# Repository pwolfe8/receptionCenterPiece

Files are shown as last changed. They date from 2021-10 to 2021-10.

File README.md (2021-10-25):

# Reception Center Piece
This was the planetary gear center piece that I designed & implemented for my reception. 

This repo is a way to share design files and provide an assembly tutorial for those who want to use this for their own reception, fork off the design, or just print their own copy of this cool decoration piece. 

## Clone this repository
Open a terminal wherever you want to place this folder. Then clone this repository and the webrepl submodule with:
```bash
git clone https://github.com/pwolfe8/receptionCenterPiece
cd receptionCenterPiece
git submodule update --init --recursive
```
___
## Mechanical
I printed this on a Prusa i3 MK3S. The trays and all the settings are in the `print_trays` folder.
I printed with [standard 1.75mm black PETG filament](<https://www.amazon.com/dp/B08XGX23TP?psc=1&ref=ppx_yo2_dt_b_product_details>) on a textured prusa print tray. 

Approximate total print time: ~19 hrs depending on heating/cooling time.

Design files can be found on Onshape: 
- [fullDesignReception](<https://cad.onshape.com/documents/7be5b9b09e066ba446a30efc/w/afbadb4d389ea6207fcba0bc/e/a346c253faa0d5286ebe5b9c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>)
- [AA_3V_Boost5V](<https://cad.onshape.com/documents/a1963687730519ec8fcaa736/w/4932db5a468bc2b8e7c12e8f/e/31f6f86f6f40c3d5acde4a41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>)

screw bolts/nuts used:
- 2x M2x8 screws ([here's](<https://www.amazon.com/gp/product/B07F739QCM/ref=ppx_yo_dt_b_search_asin_title?ie=UTF8&th=1>) the metric screw bolt/washer/nut kit I used. good to have around for various projects)
- 2x M2 nuts from same kit
- the small philips head screw that came with the microservo

## Painting & Decoration
I did not do the painting/decoration my wife and her sister did. My wife also came up with the concept. 

The premise for painting was paint a thin copper layer leaving some black showing underneath to look like worn copper for more of a steampunk feel. 
DO NOT print the smooth interface between the ring gear and the sun/planetary gears as it will add too much friction to move easily. 

Here's a quick DO NOT paint list: 
- bottom of planetary gears
- bottom of sun gear
- part of ring gear touching the bottom of the planetary/sun gears
- the base drive gear & anything used to hold it in place as it's hidden underneath anyways
- the servo horn attachment (it's hidden as well)

Decoration involved several amazon and hobby lobby items and is really up to you. [insert picture here later of ours decorated]

## Electrical

Wanted to try out micropython so I got these [D1 Mini modules](<https://www.amazon.com/dp/B08QZ2887K?psc=1&ref=ppx_yo2_dt_b_product_details>) based on the ESP8266 and flashed them with the latest version. They averaged 3 dollars each at the time I purchased them. 

If you just care about You can use any microcontroller and make your own electronics box for it as long as
- powerable off 5V since that's what the boost converter output is. (and servo needs 5V pwr). though you could power off 3V directly from battery if you modify the circuit
- has a pwm pin to drive servo

Anyways here's the parts list to make a single center piece: 
- 1x [microcontroller](<https://www.amazon.com/dp/B08QZ2887K?psc=1&ref=ppx_yo2_dt_b_product_details>) (D1 mini)
- 1x [micro servo](<https://www.amazon.com/dp/B07L2SF3R4?psc=1&ref=ppx_yo2_dt_b_product_details>) (modified for continuous rotation. you can just buy one that's continuous to make your life easier. only slightly pricier though. In the improved version I will make it based off of a continuous one.)
- 1x [5V 1A boost converter](<https://www.adafruit.com/product/4654>)(adafruit/digikey): This might've been more current than needed, but was better to be safe for a rapid prototype)
- 1x [mechanical switch](<https://www.adafruit.com/product/3221>)(adafruit): just a cool clickly mechanical switch
- 2x [battery contact positive](<https://www.digikey.com/en/products/detail/mpd-memory-protection-devices/SN-T5-2/2439587>)(digikey)
- 2x [battery contact negative](<https://www.digikey.com/en/products/detail/mpd-memory-protection-devices/SN-T5-1/2439583>)(digikey)
- the screw bolts/nuts listed in the mechanical section

and here's the schematic (full fritzing file in the circuit folder): 
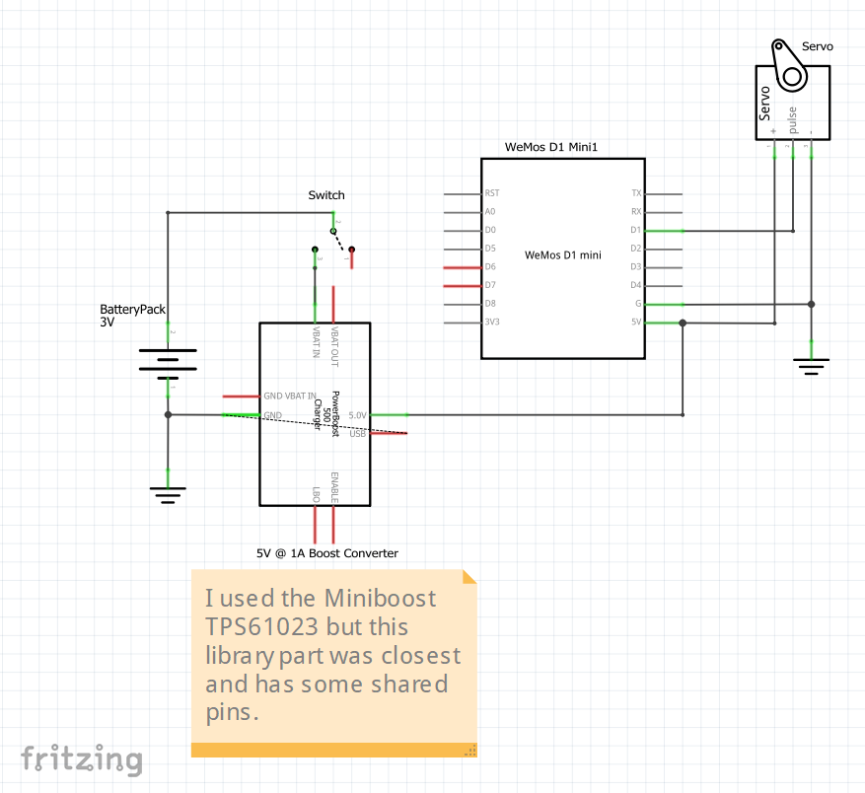
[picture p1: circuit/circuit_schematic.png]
circuit_schematic


### Servo Modification for Continuous Rotation

I was a dumbass and bought normal servos with limited range. For a little more money you can buy continuous servos in the same shape. I will post a link once I try some to make sure they have the same dimensions...

But if you really don't want to wait, here's a guide on what I did to modify the servo and the servo horn:
Maybe wear gloves to avoid silicon grease on you.
- unscrew the 4 screws
- place the gears out in the order you took them off so you don't forget
- remove the metal blocking component off the potentiometer
- replace the gears in order except the last top one
- clip the plastic blocking part off with flush cutters and smooth with exacto knife
- replace top gear and screw back together
- then take the cross shaped servo horn and chip away until you snip off the long sides with flush cutters. then make a smooth curve with flush cutters.
- use the small philips screw to hold the horn in

## Firmware/Software
[This Guide](software/D1_tutorial.md) will show you how to install the tools to flash and setup your D1 Mini for over the air updates.

I also included the version of micropython I used for this board already downloaded in the software folder [here](software/esp8266-20210902-v1.17.bin). Follow the guide to flash it on your board and send over the main.py for this center piece heartbeat pulse code.

___
## Assembly
Once you have all the pieces printed, follow this guide on assembly.
Note: pull up the onshape as a visual reference for the fully assembled piece. feel free to hide/show parts to see internals if it's unclear.

### Mechanical Assembly

Clean up the brims off all the pieces, especially the gears that will be interfacing with other gears. If you experience jamming it's probably because you haven't fully cleaned the brim off every tooth of one of the gears.

First assemble the base & motor box:
- get the base support piece and the motor box and pegs.
- align the motor box appropriately to base following the onshape design.
- now make sure the motor box and base have a shared flat surface on the bottom. feel free to put on a table to see if it's level
- then push/wiggle the pegs into place (friction fit) to hold the motor box to the base. you may have to sand/trim the hole/pegs
- Now attach the servo motor with M2 screws/nuts. I used M2x8 but you can take up to M2x12 as well. screw head coming from underneath motor box and nut on top of motor.  
NOTE: there are 2 orientations, make sure the way you choose gets the servo horn aligned with the center of the box. Not the other way
- now undo the small philips head on the servo, put the gear attachment over the servo horn, and then screw the small philips back in.

Now assemble the drive gear:
- stack the drive gear + ring gear + sun gear as shown in the cad design files.
- put the drive shaft through such that the top circle stopper is stopped against the sun gear.
- put the locking ring and shaft through to make sure it's held in place. 
- pull the ring gear away from the drive gear so they no longer contact other than by the drive shaft (should be ~2mm gap)

Place the drive gear assembly on the base by aligning the 2 small notches on the outside of the ring gear with the base. If it doesn't fit you've put your motor on in the wrong orientation so reverse/repeat steps to flip it.  Congrats! hard part done

Now assemble the platforms/planetry gear pieces.

Let's assemble the first/shortest platform first.
- find the 3 candle holders, first platform, shortest shaft, and 1 planetary gear
- get the shortest candle holder and place it in first then go clockwise like in the onshape and put the next highest, then tallest in. refer to onshape if you get stuck.
- now put the shortest shaft into the bottom shaft hole.
- then place the planetary gear onto the other side of the shaft

Next 2 platforms are straight forward: 
- get 2nd platform (feel free to hot glue some decorations on first, just make sure it's close enough balanced weight-wise for stability)
- get the middle length shaft and a planetary gear
- insert shaft into 2nd platform shaft hole and planetary gear shaft hole
- repeat for 3rd platform

Now final assembly before electrical box:
- place the 1st platform assembly inbetween sun & ring gear
- place the 2nd platform assembly 120 degrees off in the same manner
- place the 3rd platform assembly 120 degrees off in the same manner

Electrical box:
- make sure the orientation matches the onshape 
- place the switch holder into the groove
- place the battery box in the large rectangle with the boost converter facing out

### Electrical Assembly/Wiring Harness
Sadly I didn't have time to make a pcb with nice connectors and all, so I twisted together some wires and hand soldered the wiring harness.  In the future I'll release a pcb design but for now here's what I did:

tools:
- some 22 gauge solid core wire
- strippers/wire cutters
- soldering iron
- heatshrink/heat gun or lighter 

I got a 22 gauge solid core wire pack with different colors off amazon

Cut the following lengths per color and strip each side:
- white: 4, 6 cm
- red: 4, 4, 6 cm  (strip one side more for twist)
- black: 5, 5, 6, 7 cm (strip one side more for twist)
- blue: 2 cm (strip to 1.5 cm insulation)
- yellow: 4 cm 

now assemble: 
- twist the longer red exposed ends together and solder
- repeat for black
- solder blue wire as battery pack series connection
- solder white wire from pack to switch using 6 cm
- solder black long wire to pack ground
- complete rest of soldering according to the circuit schematic above

afterwards you can use a label maker to label on/off depending on how you wired it to the switch

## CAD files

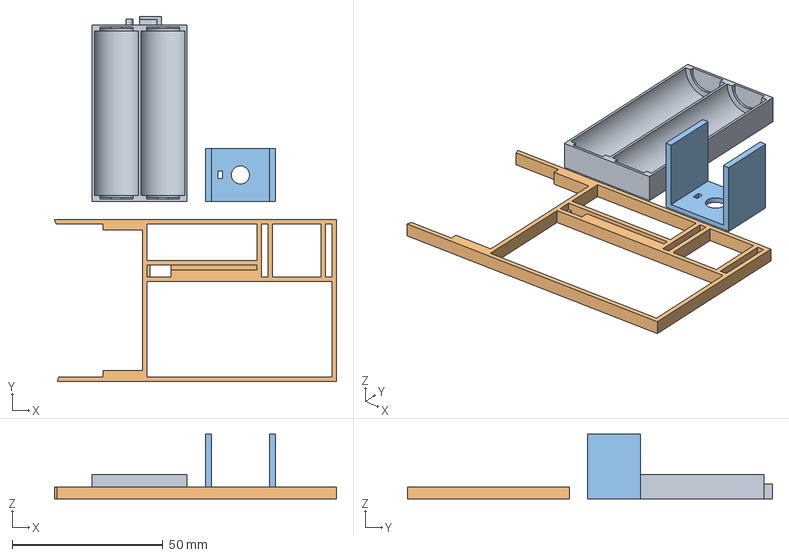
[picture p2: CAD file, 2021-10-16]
print_trays/electrical_1.2hrs_14g.3mf
93.7 x 121.1 x 21.5 mm
AA_3V (2).stl
electrical_box.stl_1
electrical_box.stl_2

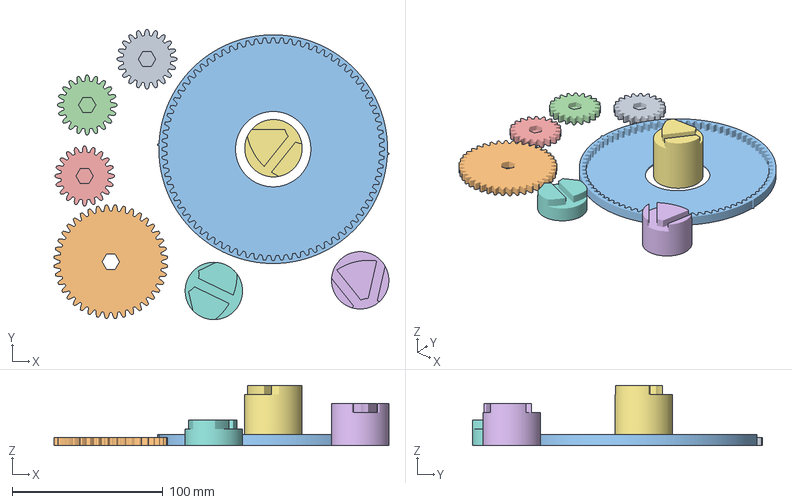
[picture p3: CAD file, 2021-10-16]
print_trays/tray2_6hrs_97g.3mf
222.4 x 192.7 x 40.0 mm
fullDesign (4).stl_10
fullDesign (4).stl_11
fullDesign (4).stl_13
fullDesign (4).stl_17
fullDesign (4).stl_23
candleHolders.stl_1
candleHolders.stl_2
candleHolders.stl_3

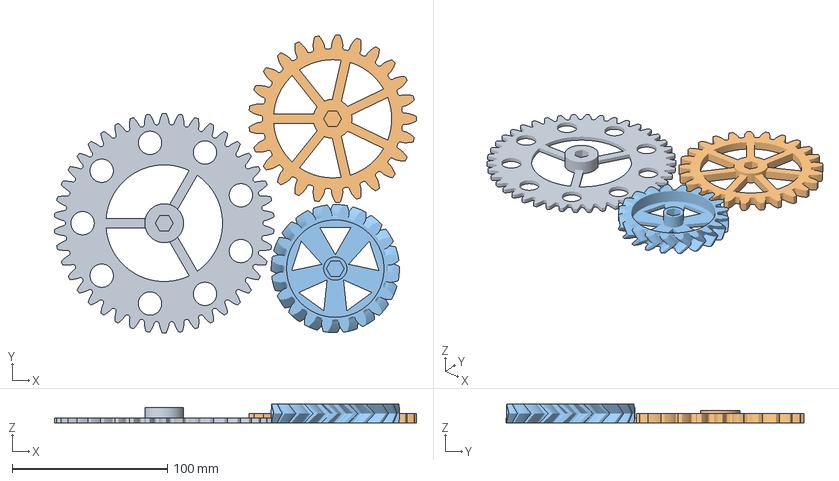
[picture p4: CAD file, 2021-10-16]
print_trays/tray3_5.5hrs_83g.3mf
232.9 x 191.9 x 12.0 mm
fullDesign (4).stl_5
fullDesign (4).stl_6
fullDesign (4).stl_8

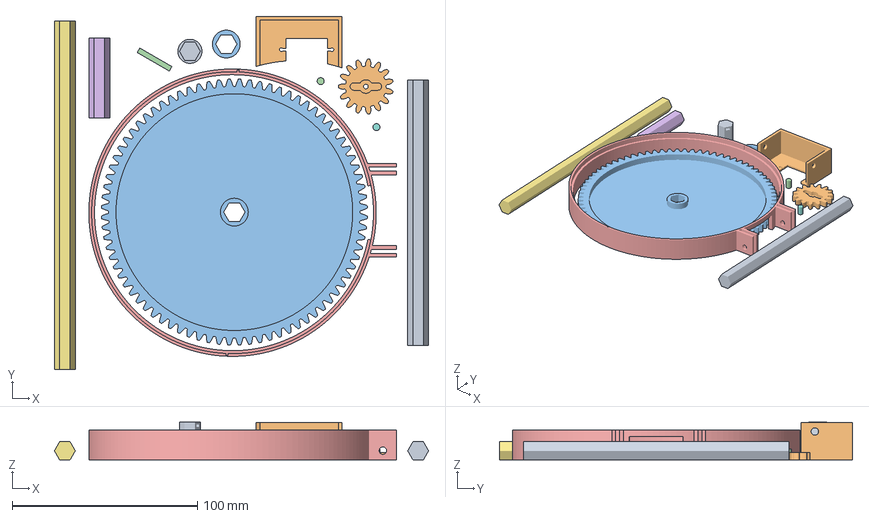
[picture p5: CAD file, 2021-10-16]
print_trays/tray1_6.5hrs_95g.3mf
201.8 x 190.4 x 20.4 mm
fullDesign (4).stl_2
fullDesign (4).stl_3
fullDesign (4).stl_4
fullDesign (4).stl_7
fullDesign (4).stl_12
fullDesign (4).stl_14
fullDesign (4).stl_16
fullDesign (4).stl_18
fullDesign (4).stl_19
fullDesign (4).stl_20
fullDesign (4).stl_21
fullDesign (4).stl_22

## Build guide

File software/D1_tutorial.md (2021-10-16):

# A Quick D1 Mini Micropython Setup/Tutorial

Just my quick reference/cheat sheet for D1 Mini board resources and setting up micropython for updating main.py remotely

## Purchase Source
bought 10 off amazon at ~3 dollars a piece [here](<https://www.amazon.com/dp/B08QZ2887K?psc=1&ref=ppx_yo2_dt_b_product_details>)

## supposed schematic and potential pinout
- https://www.wemos.cc/en/latest/_static/files/sch_d1_mini_v3.0.0.pdf
- https://www.wemos.cc/en/latest/d1/d1_mini.html
- https://escapequotes.net/esp8266-wemos-d1-mini-pins-and-diagram/

## Flashing ESP8266 with Latest Micropython
[tutorial source](<https://www.wemos.cc/en/latest/tutorials/d1/get_started_with_micropython_d1.html>)

Find the latest micropython .bin file in the >4MB flash section and download it [here](<https://micropython.org/download/esp8266/>)
install esptool on your python with `pip install esptool` (github [here](<https://github.com/espressif/esptool>) if you want)

Plug in device via USB and check the port name in device manager (example: COM6)
Now swap PORT_NAME with your port and FIRMWARE.bin with the .bin file you just downloaded in the following commands:
```bash
# first erase flash
esptool.py --port PORT_NAME erase_flash

# then write flash with your preferred firmware .bin file 
esptool.py --port PORT_NAME --baud 115200 write_flash --flash_size=4MB -fm dio 0 FIRMWARE.bin

# here's the example command I used in powershell for the version in this repo. it assumes you're already in the software folder and COM6 is your device serial port
esptool.py --port COM6 --baud 115200 write_flash --flash_size=4MB -fm dio 0 .\esp8266-20210902-v1.17.bin
```

Open [realterm](https://sourceforge.net/projects/realterm/) and set baud to 115200 and open your port. you should be able to type help() and follow the first steps now

## First Steps
```python
# this is how to get help
help()

# this sets up a remote accessible micropython shell
# follow prompts after import to enable webrepl on boot (feel free to reboot)
import webrepl_setup

# this is how to check what files exist on the board
import os
os.listdir()
```

## Network Config
[tutorial source](<https://docs.micropython.org/en/latest/esp8266/tutorial/network_basics.html>)
```python
# turn on client connection and turn off access point
import network
sta_if = network.WLAN(network.STA_IF)
ap_if = network.WLAN(network.AP_IF)
sta_if.active(True)
ap_if.active(False)

# check to be sure they're on/off
sta_if.active()
ap_if.active()

# get mac address
import ubinascii
ubinascii.hexlify(sta_if.config('mac'),':').decode()

# connect to your router's SSID with password now 
sta_if.connect('ssidgoeshere','passwordgoeshere')
# keep checking for a minute until connected
sta_if.isconnected()
# see ip address & network info
sta_if.ifconfig()
```

## webrepl push/pull
navigate your terminal into the webrepl submodule folder first
```bash
# example pull (just pulls the boot.py from remote and saves to local file named "local_boot.py")
python .\webrepl_cli.py -p YOURPASSWORDHERE REMOTEIPHERE:boot.py local_boot.py

# example push (just pushes your local file main.py file located one directory above the cloned webrepl folder to your board and names it main.py)
python .\webrepl_cli.py -p YOURPASSWORDHERE ../software/main.py REMOTEIPHERE:main.py

# feel free to setup batch/bash scripts for your common operations
```

## `main.py` 
micropython executes main.py (if it exists) after boot.py so I generally put my code updates here.
Let's setup an example main.py to turn on the onboard LED. It's connected to GPIO2 according to the D1 Mini Schematic in an active pull down configuration.

Here's an example main.py to turn the LED on on boot

```python
import machine
pin = machine.Pin(2, machine.Pin.OUT)
pin.off()
```

If you want to change the syntax so "on" turns led on use [this documentation](<https://docs.micropython.org/en/latest/library/machine.Signal.html>)

Now use the example push as reference to push this `main.py` file to your board:
```bash
python .\webrepl_cli.py -p YOURPASSWORDHERE ../software/main.py REMOTEIPHERE:main.py
```

To reset your board to let the main.py changes take effect:
- open the webrepl/webrepl.html file in your browser, connect to your W1 Mini's ip address
- type
    ```python
    import machine
    machine.reset()
    ```

Feel free to modify this main.py to your heart's content and push updates/pull current files.
Happy Hacking

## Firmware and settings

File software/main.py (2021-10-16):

# main.py
import machine
import time
import math

servoState = False
servoPulseIdx = 0
threeCountWait = 0

def pulse(l, t):
    for i in range(20):
        l.duty(int(math.sin(i / 10 * math.pi) * 500 + 500))
        time.sleep_ms(t)

def heartbeat(pinpwm, pulseCount):
    heartbeat_delay_ms = 250
    for c in range(pulseCount):
        pulse(pinpwm, 80)
        time.sleep_ms(heartbeat_delay_ms)

def togglepin(p):
    if p.value() == 0:
        p.on()
    elif p.value() == 1:
        p.off()

def debounce(p):
    '''debounce a button pin'''
    window_length_ms = 100
    s = 0
    for i in range(window_length_ms):
        s += p.value()
        time.sleep_ms(1)
    return round(s/window_length_ms)

# def toggleServo():
#     global servoState
#     servoState = not servoState
#     if servoState:
#         servoLEDpin.on()
#     else:
#         servoLEDpin.off()

# def servoButtonCallback(p):
#     val = debounce(p)
#     if val == 0:
#         toggleServo()

def runServoHeartbeat():
    global servoPulseIdx
    global threeCountWait
    if servoPulseIdx >= 20:
        threeCountWait += 1
        # servopwm.duty(0)
        if threeCountWait >= 3:
            threeCountWait = 0
            servoPulseIdx = 0
    else:
        servopwm.duty(int(math.sin(servoPulseIdx / 10 * math.pi) * 500 + 500))
        servoPulseIdx += 1

def blockingHeartbeat():
    pulse(servopwm, 80)

def timerCallback(t):
    blockingHeartbeat()

# onboard LED setup
boardLEDpin = machine.Pin(2, machine.Pin.OUT)
boardLEDpin.off() # this turns on board LED since active low

# servo button, led, and pwm setup
# servobutton = machine.Pin(12, machine.Pin.IN, machine.Pin.PULL_UP)
# servobutton.irq(trigger=machine.Pin.IRQ_FALLING, handler=servoButtonCallback)
# servoLEDpin = machine.Pin(13, machine.Pin.OUT)
# servoLEDpin.off() # active high. start off though.
servopwm = machine.PWM(machine.Pin(5), freq=50) # GPIO5 is D1 on the mini

# servo timer loop setup
servoLoopPeriod_ms = 1850
servoTimer = machine.Timer(-1)
servoTimer.init(period=servoLoopPeriod_ms, mode=machine.Timer.PERIODIC, callback=timerCallback)

### heartbeat tests ###
# pulseCount = 25
## led heartbeat test
# ledpwm = machine.PWM(ledpin, freq=50)
# heartbeat(ledpwm, pulseCount)
## servo heartbeat
# block_webrepl = True
# while True and block_webrepl:
#     heartbeat(servopwm, 25)

## socket server backdoor testing
# import socket 
# import sys 
# s = socket.socket(socket.AF_INET, socket.SOCK_DGRAM)
# s.bind('10.160.0.105', 6969)
# while True:
#     data, addr = s.recvfrom(1024)
#     if data == b'hello there':
#         jamSignal = True
#         togglepin(boardLEDpin)
#         time.sleep(2)
#     data = ''

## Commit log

2021-10-16 pushing mechanical files/tutorial
    [tray1_6.5hrs_95g.3mf, tray2_6hrs_97g.3mf, tray3_5.5hrs_83g.3mf]
2021-10-16 added the electrical box files too
    [electrical_box_40m_7g.3mf]
2021-10-16 fleshing out the readme more and renamed mechanical folder to print_trays
    [electrical_box_40m_7g.3mf, tray1_6.5hrs_95g.3mf, tray2_6hrs_97g.3mf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]
2021-10-16 added do not paint list
    [electrical_box_0.7hrs_7g.3mf]
2021-10-16 added in battery holder and electrical parts list
    [electrical_1.2hrs_14g.3mf, electrical_box_0.7hrs_7g.3mf]
2021-10-16 added servo modifications until I can find an appropriate continuous micro rotation servo of similar dimensions. or i'll just release an improved version in the next month or so
2021-10-16 added circuit schematic
    [electronics.fzz]
2021-10-16 added software/guide and reorganized. just a little more cleanup left
    [electronics.fzz]
2021-10-17 finished mechanical assembly instructions
